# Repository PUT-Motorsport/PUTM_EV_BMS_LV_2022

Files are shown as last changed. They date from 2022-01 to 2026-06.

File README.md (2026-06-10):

# PUTM_EV_BMS_LV

## About
Battery Management System (BMS) is an electronic system that manages a rechargeable battery. In case of this project, it will be battery made of 21700 cells packed in 6S2P configuration.

## Tasks of Battery Management System:
- Voltage Measurement on every cell
- Current Measurement
- Temperature Measurement
- State of Charge calculate
- Charge Management with Cell Balance System
- Error Handling based on FSG Rules
- CAN - CAR communication
- Serial data print through USB

## Block diagram of the firmware

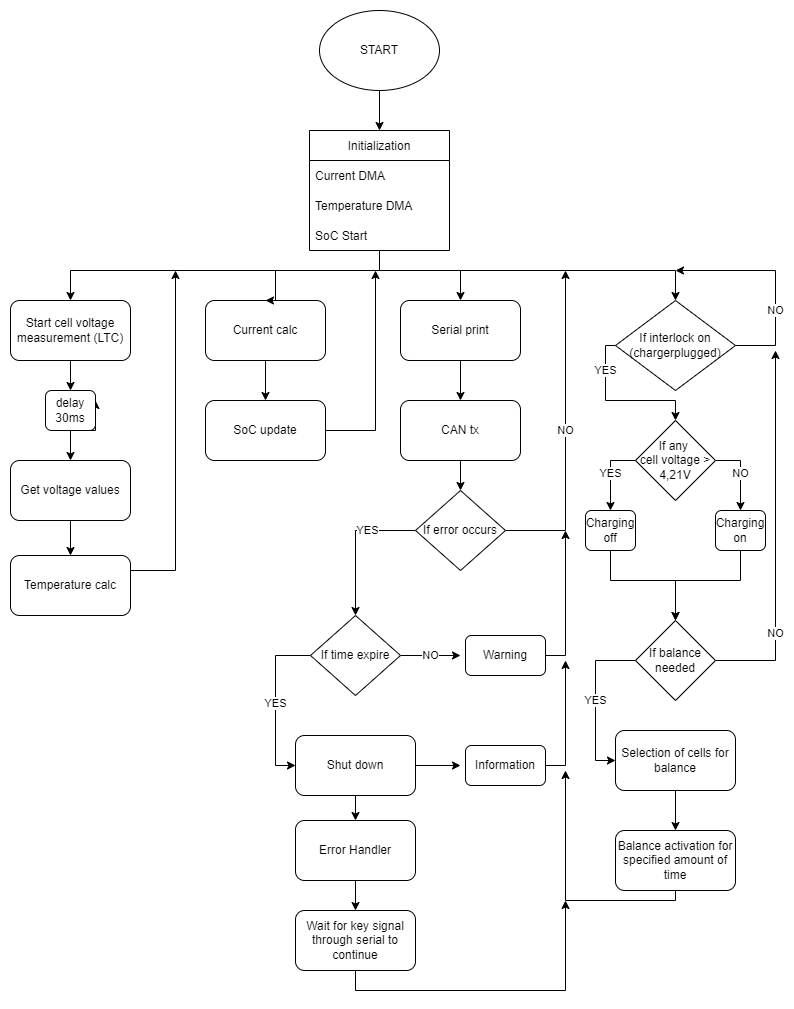
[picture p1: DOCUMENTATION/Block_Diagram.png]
diagram


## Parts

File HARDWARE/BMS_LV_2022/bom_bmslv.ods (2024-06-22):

Name | Value | Qty
Cell | 21700 | 12
Capacitor | 100nF | 22
Capacitor | 22pF | 2
Capacitor | 10uF | 2
Capacitor | 1uF | 7
Capacitor | 10nF | 7
Capacitor | 330pF | 1
Capacitor | 47nF | 1
Capacitor | 2.2uF | 1
Capacitor | 100uF | 1
Capacitor | 1nF | 1
LED | LED_RED | 10
Diode | PESD2CAN.215 | 1
Diode | D_Zener 9.1V | 6
Diode | D_TVS | 1
Diode | D_Schottky | 1
Fuse | PPTC 200mA | 1
Fuse Holder | Fuse Holder 10A | 2
Fuse | Fuse 10A
Ferrite Bead | 60R@100MHz | 3
Connector | USB-C_GCT_USB4145-03-0070-C | 1
Connector | D38999/20WD97SN | 1
Connector | B9B-XH-A (LF)(SN) | 1
Connector | XHP-9 | 1
Connector | 200-FTSH-107-01-L-DV-K-A | 1
Connector | B7B-XH-A (LF)(SN) | 1
Connector | XHP-7 | 1
Inductor | 10uH | 1
Inductor | 22uH | 1
LTC68101 | LTC6810-2 | 1
Transistor | BC846 | 1
Transistor | ZXMN3F30FHTA | 6
Transistor | SiSS05DN | 4
Transistor | BSS138 | 1
Resistor | 100k | 2
Resistor | 470 | 4
Resistor | 120 | 1
Resistor | 30 | 4
Resistor | 100 | 11
Resistor | 10k | 11
Resistor | 1k | 8
Resistor | 2.2k | 4
Resistor | 10 | 12
Resistor | 330 | 6
Resistor | 88.7k | 1
Resistor | 22.1k | 1
Resistor | 20k | 1
Resistor | 2.7k | 1
Resistor | 2k | 1
Resistor | 5.1k | 2
Tactile Switch | B3U-3000PM | 1
Thermistor_NTC | B57861S0103F040 | 8
MCU | STM32L4P5RET6 | 1
Switching Voltage Regulators | LD3985M33R_TSOT23 | 1
LDO | LMR23610 | 1
CAN transceiver | ATA6561-GAQW-N | 1
Current Sensor | ACHS-7123 | 1
Quartz Crystal | Quartz 16MHz | 1

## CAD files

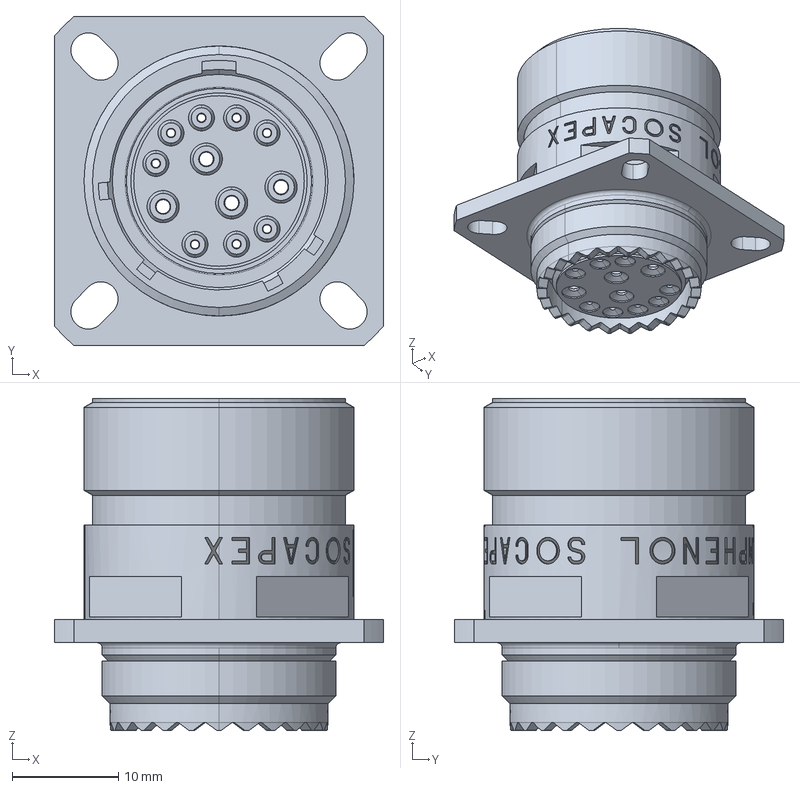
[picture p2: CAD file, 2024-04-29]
HARDWARE/BMS_LV_2022/3Dmodels/tvp00rw15-97p.stp
31.0 x 31.0 x 31.3 mm

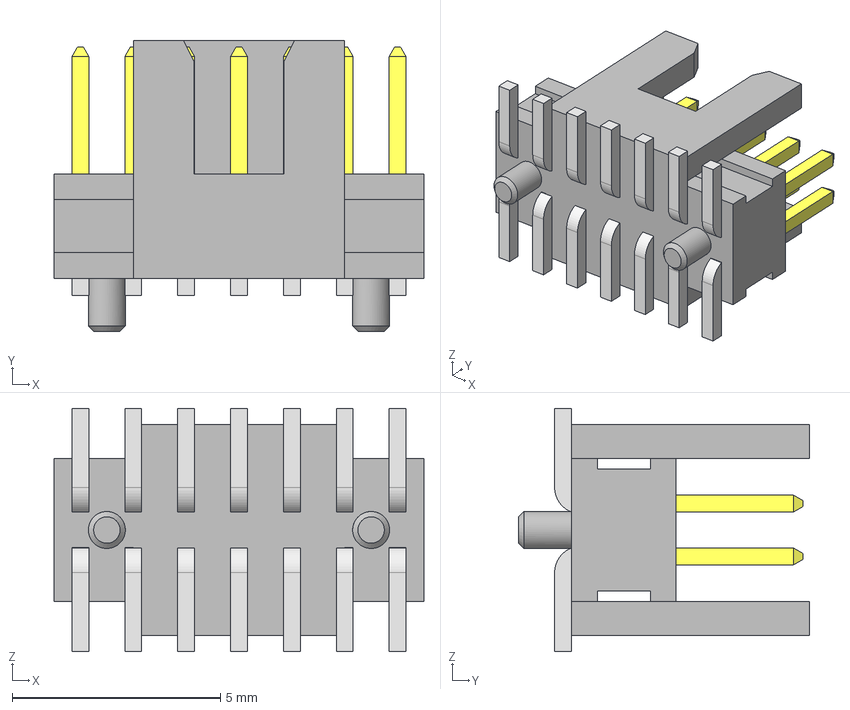
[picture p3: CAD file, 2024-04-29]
HARDWARE/BMS_LV_2022/3Dmodels/FTSH-107-01-L-DV-K-A.stp
8.89 x 6.98 x 5.84 mm
FTSH-107-01-L-DV-K-A_pins2
FTSH-107-01-L-DV-K-A_pins1
FTSH-107-01-L-DV-K-A_body

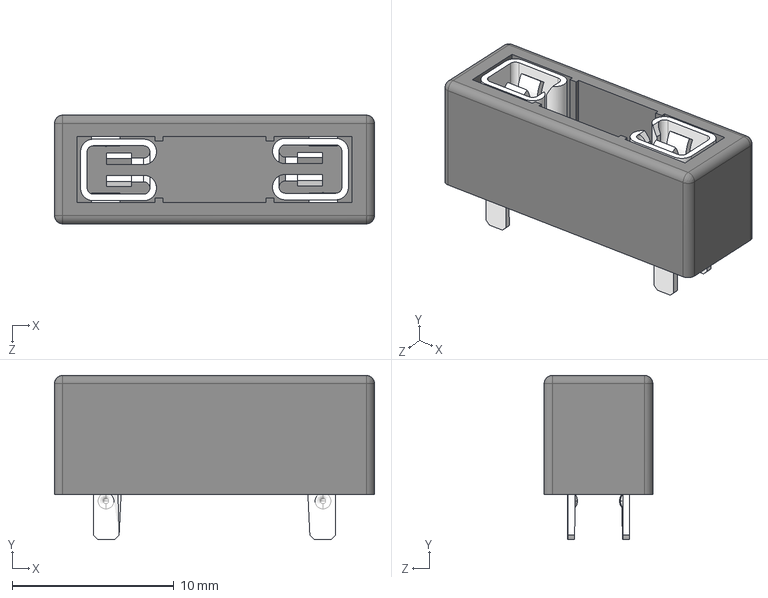
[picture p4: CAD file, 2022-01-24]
HARDWARE/BMS_LV_2022/3Dmodels/3557-2.stp
19.8 x 10.2 x 6.73 mm

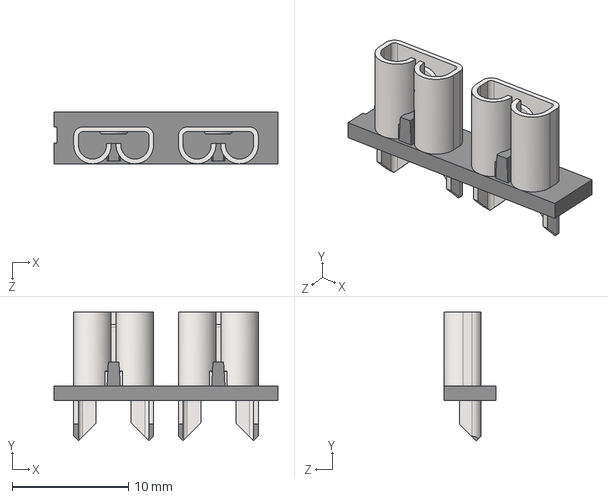
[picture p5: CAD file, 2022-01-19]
HARDWARE/BMS_LV_2022/3Dmodels/3522-2.stp
19.3 x 11.1 x 4.44 mm

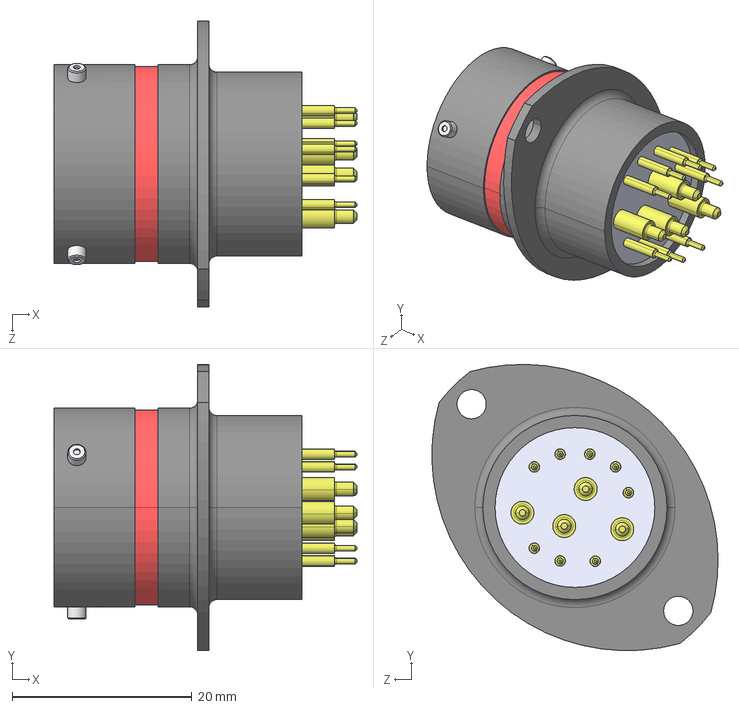
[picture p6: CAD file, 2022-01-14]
HARDWARE/BMS_LV_2022/3Dmodels/AS214-97PN.STEP
33.7 x 31.8 x 31.8 mm

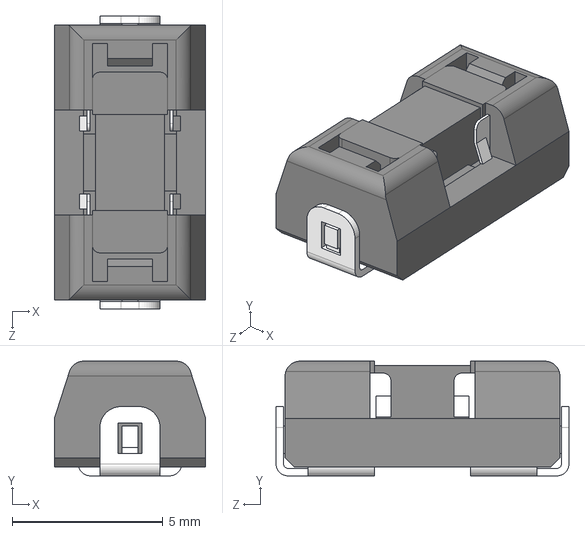
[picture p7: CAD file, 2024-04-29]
HARDWARE/BMS_LV_2022/3Dmodels/0154010.DR.stp
5.03 x 3.81 x 9.73 mm

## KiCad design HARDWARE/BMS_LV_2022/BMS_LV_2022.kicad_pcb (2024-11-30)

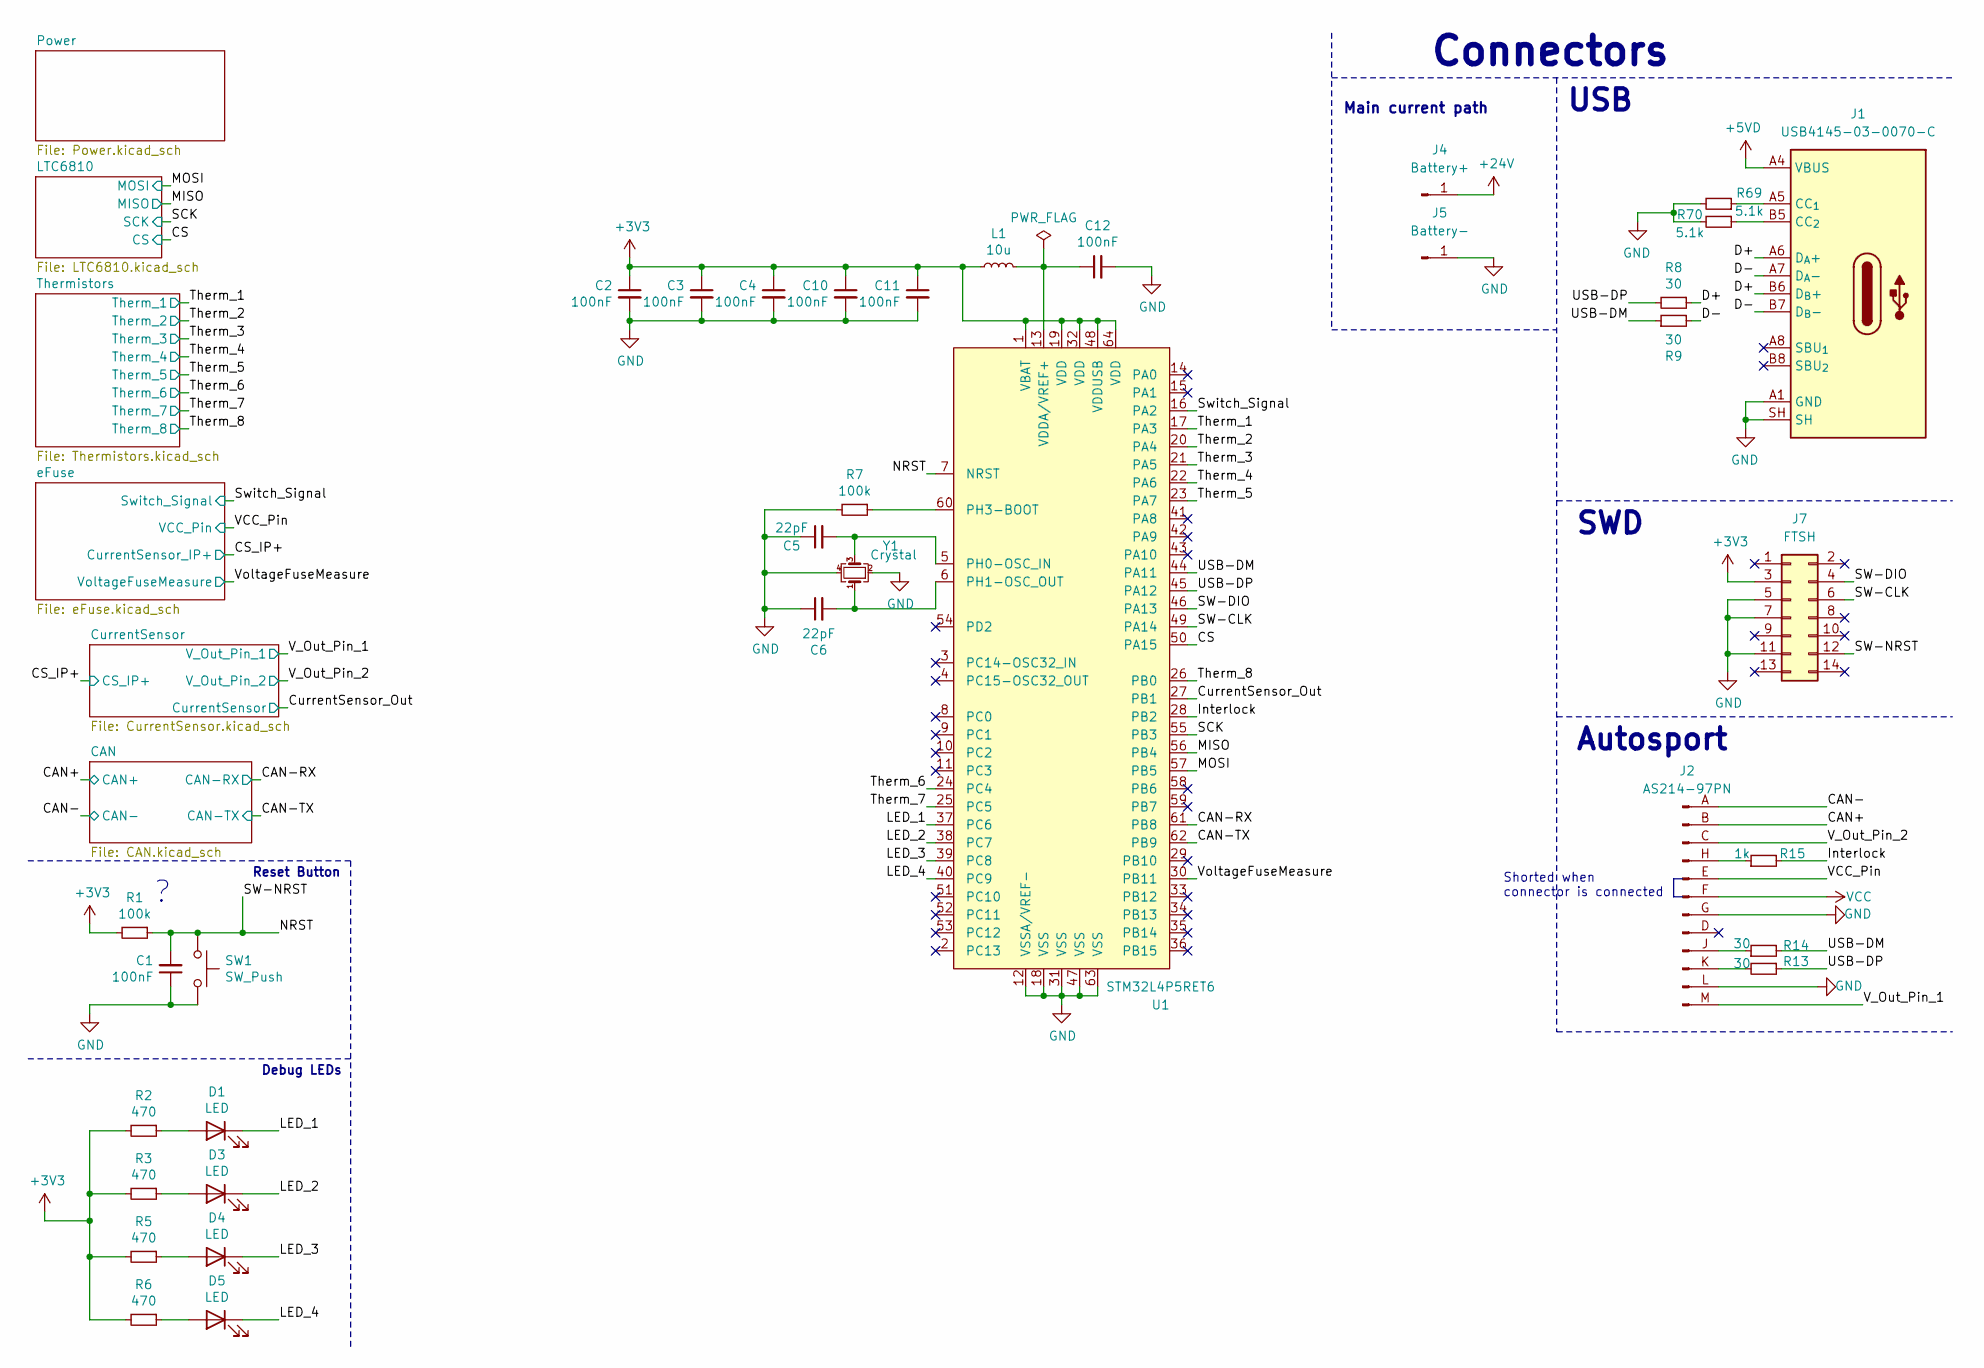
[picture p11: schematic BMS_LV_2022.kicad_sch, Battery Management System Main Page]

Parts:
C1, C2, C3, C4, C10, C11, C12: 100nF; C_0603_1608Metric
C5, C6: 22pF; C_0603_1608Metric
D1, D3, D4, D5: LED; LED_0603_1608Metric
J1: USB-C_GCT_USB4145-03-0070-C; USB-C_Receptacle_GCT_USB4145-03-0070-C; MPN USB4145-03-0070-C
J2: AS214-97PN
J4: Battery+; CellPad
J5: Battery-; CellPad
J7: FTSH; FTSH-107-XX-YYY-DV-K-A; Mouser Part Number 200-FTSH10701LDVKA
L1: 10u; L_0603_1608Metric
R1, R7: 100k; R_0603_1608Metric
R2, R3, R5, R6: 470; R_0603_1608Metric
R8, R9, R13, R14: 30; R_0603_1608Metric
R15: 1k; R_0603_1608Metric
R69, R70: 5.1k; R_0603_1608Metric
SW1: SW_Push; SW_SPST_B3U-1000P; Part Number B3U-1000PM
U1: STM32L4P5RET6; LQFP-64_10x10mm_P0.5mm
Y1: Crystal; Crystal_SMD_3225-4Pin_3.2x2.5mm

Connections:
+3V3: C2.1, C3.1, C4.1, C10.1, C11.1, J7.3, L1.2, R1.2, R2.2, R3.2, R5.2, R6.2, U1.1 (VBAT), U1.19 (VDD), U1.32 (VDD), U1.48 (VDDUSB), U1.64 (VDD); also elsewhere on the board
+5VD: J1.A4 (VBUS), J1.A9 (VBUS), J1.B4 (VBUS), J1.B9 (VBUS); also elsewhere on the board
+24V: J4.1; also elsewhere on the board
/CAN+: J2.B; also elsewhere on the board
/CAN-: J2.A; also elsewhere on the board
/CAN-RX: U1.61 (PB8); also elsewhere on the board
/CAN-TX: U1.62 (PB9); also elsewhere on the board
/CS: U1.50 (PA15); also elsewhere on the board
/CurrentSensor_Out: U1.27 (PB1); also elsewhere on the board
/D+: J1.A6 (D_{A}+), J1.B6 (D_{B}+), R8.1
/D-: J1.A7 (D_{A}-), J1.B7 (D_{B}-), R9.2
/Interlock: R15.2, U1.28 (PB2)
/LED_1: D1.1 (K), U1.37 (PC6)
/LED_2: D3.1 (K), U1.38 (PC7)
/LED_3: D4.1 (K), U1.39 (PC8)
/LED_4: D5.1 (K), U1.40 (PC9)
/MISO: U1.56 (PB4); also elsewhere on the board
/MOSI: U1.57 (PB5); also elsewhere on the board
/NRST: C1.2, J7.12, R1.1, SW1.1, U1.7 (NRST)
/SCK: U1.55 (PB3); also elsewhere on the board
/SW-CLK: J7.6, U1.49 (PA14)
/SW-DIO: J7.4, U1.46 (PA13)
/Switch_Signal: U1.16 (PA2); also elsewhere on the board
/Therm_1: U1.17 (PA3); also elsewhere on the board
/Therm_2: U1.20 (PA4); also elsewhere on the board
/Therm_3: U1.21 (PA5); also elsewhere on the board
/Therm_4: U1.22 (PA6); also elsewhere on the board
/Therm_5: U1.23 (PA7); also elsewhere on the board
/Therm_6: U1.24 (PC4); also elsewhere on the board
/Therm_7: U1.25 (PC5); also elsewhere on the board
/Therm_8: U1.26 (PB0); also elsewhere on the board
/USB-DM: R9.1, R14.2, U1.44 (PA11)
/USB-DP: R8.2, R13.1, U1.45 (PA12)
/VCC_Pin: J2.E; also elsewhere on the board
/V_Out_Pin_1: J2.M; also elsewhere on the board
/V_Out_Pin_2: J2.C; also elsewhere on the board
/VoltageFuseMeasure: U1.30 (PB11); also elsewhere on the board
GND: C1.1, C2.2, C3.2, C4.2, C5.1, C6.1, C10.2, C11.2, C12.2, J1.A1 (GND), J1.A12 (GND), J1.B1 (GND), J1.B12 (GND), J1.SH, J2.G, J2.L, J5.1, J7.5, J7.7, J7.11, R7.2, R69.2, R70.2, SW1.2, U1.12 (VSSA/VREF-), U1.18 (VSS), U1.31 (VSS), U1.47 (VSS), U1.63 (VSS), Y1.2, Y1.4; also elsewhere on the board
unnamed: D1.2 (A), R2.1
unnamed: D3.2 (A), R3.1
unnamed: D4.2 (A), R5.1
unnamed: D5.2 (A), R6.1
unnamed: J1.A5 (CC_{1}), R69.1
unnamed: J1.B5 (CC_{2}), R70.1
unnamed: J2.H, R15.1
unnamed: J2.J, R14.1
unnamed: J2.K, R13.2
unnamed: C5.2, U1.5 (PH0-OSC_IN), Y1.3
unnamed: C6.2, U1.6 (PH1-OSC_OUT), Y1.1
unnamed: R7.1, U1.60 (PH3-BOOT)
unnamed: C12.1, L1.1, U1.13 (VDDA/VREF+)
VCC: J2.F; also elsewhere on the board

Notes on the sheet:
SWD
USB
Debug LEDs
Reset Button
Main current path
Shorted when connector is connected
Connectors
Autosport

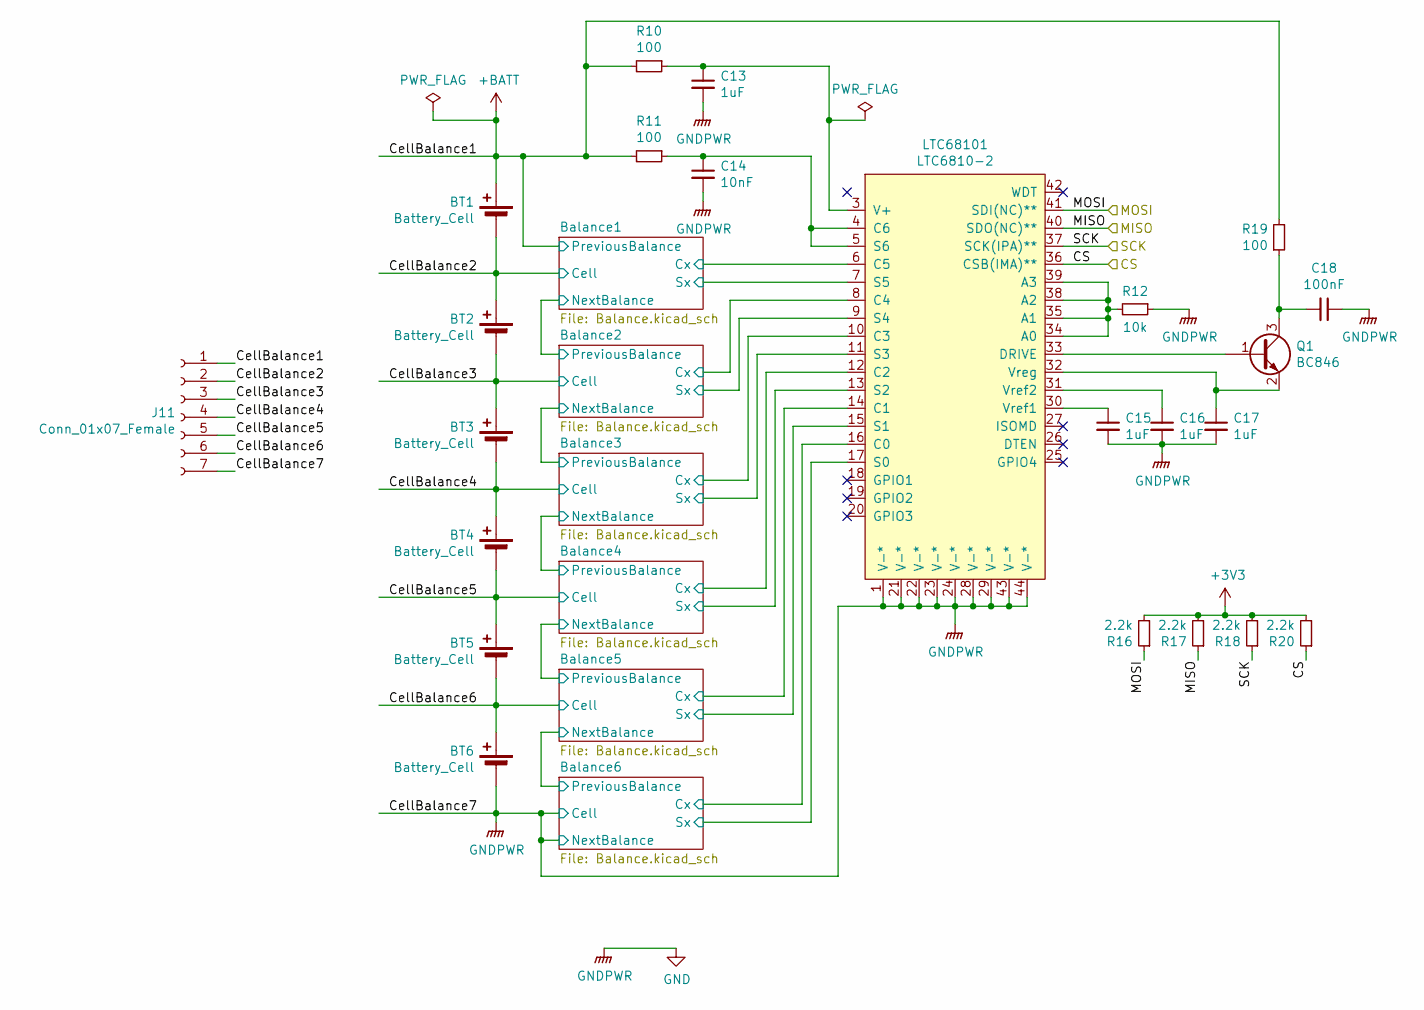
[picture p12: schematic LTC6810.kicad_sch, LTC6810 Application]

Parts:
BT1, BT2, BT3, BT4, BT5, BT6: Battery_Cell
C13, C15, C16, C17: 1uF; C_0603_1608Metric
C14: 10nF; C_0603_1608Metric
C18: 100nF; C_0603_1608Metric
J11: Conn_01x07_Female; JST_XH_B7B-XH-A_1x07_P2.50mm_Vertical
LTC68101: LTC6810-2; LTC6810
Q1: BC846; SOT-23
R10, R11, R19: 100; R_0603_1608Metric
R12: 10k; R_0603_1608Metric
R16, R17, R18, R20: 2.2k; R_0603_1608Metric

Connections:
+3V3: R16.2, R17.2, R18.2, R20.2; also elsewhere on the board
+BATT: BT1.1 (+), J11.1, R10.2, R11.2, R19.2; also elsewhere on the board
/CS: LTC68101.36 (CSB(IMA)**), R20.1; also elsewhere on the board
/LTC6810/Balance1/Cx: LTC68101.6 (C5); also elsewhere on the board
/LTC6810/Balance1/Sx: LTC68101.7 (S5); also elsewhere on the board
/LTC6810/Balance2/Cx: LTC68101.8 (C4); also elsewhere on the board
/LTC6810/Balance2/Sx: LTC68101.9 (S4); also elsewhere on the board
/LTC6810/Balance3/Cx: LTC68101.10 (C3); also elsewhere on the board
/LTC6810/Balance3/Sx: LTC68101.11 (S3); also elsewhere on the board
/LTC6810/Balance4/Cx: LTC68101.12 (C2); also elsewhere on the board
/LTC6810/Balance4/Sx: LTC68101.13 (S2); also elsewhere on the board
/LTC6810/Balance5/Cx: LTC68101.14 (C1); also elsewhere on the board
/LTC6810/Balance5/Sx: LTC68101.15 (S1); also elsewhere on the board
/LTC6810/Balance6/Cx: LTC68101.16 (C0); also elsewhere on the board
/LTC6810/Balance6/Sx: LTC68101.17 (S0); also elsewhere on the board
/LTC6810/CellBalance2: BT1.2 (-), BT2.1 (+), J11.2; also elsewhere on the board
/LTC6810/CellBalance3: BT2.2 (-), BT3.1 (+), J11.3; also elsewhere on the board
/LTC6810/CellBalance4: BT3.2 (-), BT4.1 (+), J11.4; also elsewhere on the board
/LTC6810/CellBalance5: BT4.2 (-), BT5.1 (+), J11.5; also elsewhere on the board
/LTC6810/CellBalance6: BT5.2 (-), BT6.1 (+), J11.6; also elsewhere on the board
/MISO: LTC68101.40 (SDO(NC)**), R17.1; also elsewhere on the board
/MOSI: LTC68101.41 (SDI(NC)**), R16.1; also elsewhere on the board
/SCK: LTC68101.37 (SCK(IPA)**), R18.1; also elsewhere on the board
GND: BT6.2 (-), C13.2, C14.2, C15.2, C16.2, C17.2, C18.1, J11.7, LTC68101.1 (V-*), LTC68101.21 (V-*), LTC68101.22 (V-*), LTC68101.23 (V-*), LTC68101.24 (V-*), LTC68101.28 (V-*), LTC68101.29 (V-*), LTC68101.43 (V-*), LTC68101.44 (V-*), R12.1; also elsewhere on the board
unnamed: LTC68101.34 (A0), LTC68101.35 (A1), LTC68101.38 (A2), LTC68101.39 (A3), R12.2
unnamed: C14.1, LTC68101.4 (C6), LTC68101.5 (S6), R11.1
unnamed: LTC68101.33 (DRIVE), Q1.1 (B)
unnamed: C13.1, LTC68101.3 (V+), R10.1
unnamed: C15.1, LTC68101.30 (Vref1)
unnamed: C16.1, LTC68101.31 (Vref2)
unnamed: C17.1, LTC68101.32 (Vreg), Q1.2 (E)
unnamed: C18.2, Q1.3 (C), R19.1

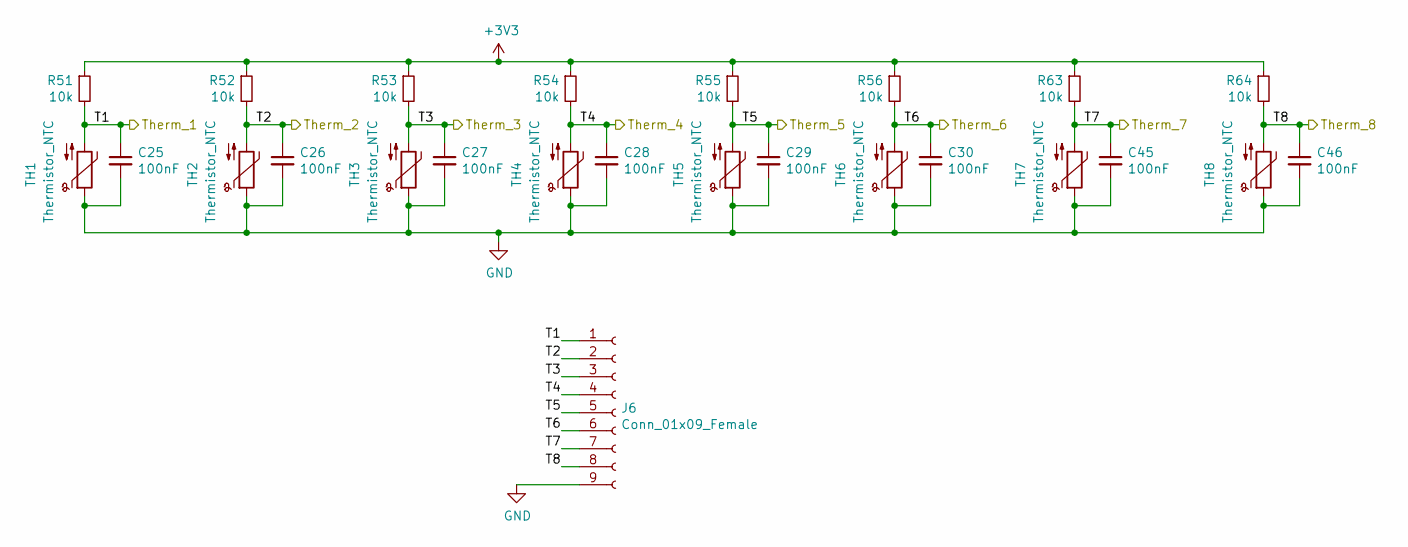
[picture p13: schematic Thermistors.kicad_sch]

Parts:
C25, C26, C27, C28, C29, C30, C45, C46: 100nF; C_0603_1608Metric
J6: Conn_01x09_Female; JST_XH_B9B-XH-A_1x09_P2.50mm_Vertical
R51, R52, R53, R54, R55, R56, R63, R64: 10k; R_0603_1608Metric
TH1, TH2, TH3, TH4, TH5, TH6, TH7, TH8: Thermistor_NTC

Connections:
+3V3: R51.1, R52.1, R53.1, R54.1, R55.1, R56.1, R63.1, R64.1; also elsewhere on the board
/Therm_1: C25.1, J6.1, R51.2, TH1.2; also elsewhere on the board
/Therm_2: C26.1, J6.2, R52.2, TH2.2; also elsewhere on the board
/Therm_3: C27.1, J6.3, R53.2, TH3.2; also elsewhere on the board
/Therm_4: C28.1, J6.4, R54.2, TH4.2; also elsewhere on the board
/Therm_5: C29.1, J6.5, R55.2, TH5.2; also elsewhere on the board
/Therm_6: C30.1, J6.6, R56.2, TH6.2; also elsewhere on the board
/Therm_7: C45.1, J6.7, R63.2, TH7.2; also elsewhere on the board
/Therm_8: C46.1, J6.8, R64.2, TH8.2; also elsewhere on the board
GND: C25.2, C26.2, C27.2, C28.2, C29.2, C30.2, C45.2, C46.2, J6.9, TH1.1, TH2.1, TH3.1, TH4.1, TH5.1, TH6.1, TH7.1, TH8.1; also elsewhere on the board

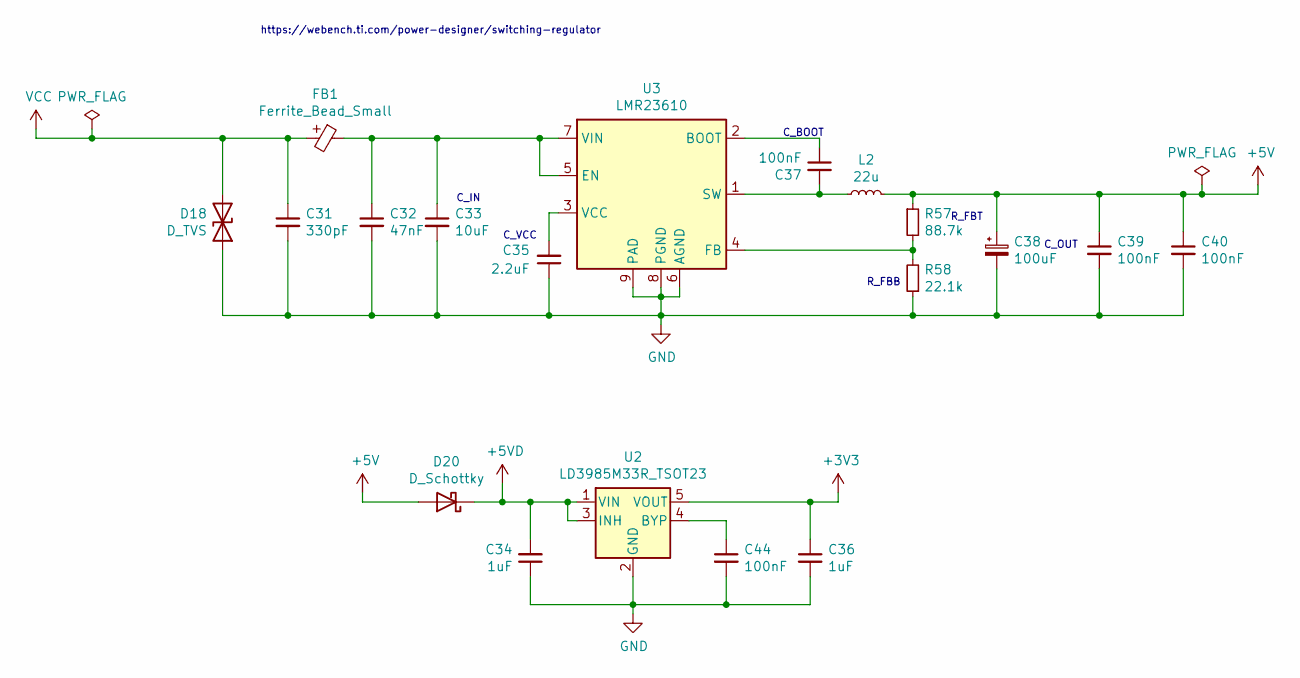
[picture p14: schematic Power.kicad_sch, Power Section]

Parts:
C31: 330pF; C_0603_1608Metric
C32: 47nF; C_0603_1608Metric
C33: 10uF; C_0603_1608Metric
C34, C36: 1uF; C_0603_1608Metric
C35: 2.2uF; C_0603_1608Metric
C37, C39, C40, C44: 100nF; C_0603_1608Metric
C38: 100uF; CP_EIA-6032-28_Kemet-C; Part Number TPSC107K010R0100
D18: D_TVS; D_SMB
D20: D_Schottky; D_SOD-123; Part Number SD103BW
FB1: Ferrite_Bead_Small; L_0603_1608Metric
L2: 22u; L_7.3x7.3_H4.5; Part Number 7447779122
R57: 88.7k; R_0603_1608Metric
R58: 22.1k; R_0603_1608Metric
U2: LD3985M33R_TSOT23; TSOT-23-5; Part Number LDS3985M33R
U3: LMR23610; Texas_HSOP-8-1EP_3.9x4.9mm_P1.27mm_ThermalVias

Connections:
+3V3: C36.1, U2.5 (VOUT); also elsewhere on the board
+5V: C38.1, C39.1, C40.1, D20.2 (A), L2.2, R57.1; also elsewhere on the board
+5VD: C34.2, D20.1 (K), U2.1 (VIN), U2.3 (INH); also elsewhere on the board
GND: C31.2, C32.2, C33.2, C34.1, C35.1, C36.2, C38.2, C39.2, C40.2, C44.2, D18.1 (A1), R58.1, U2.2 (GND), U3.6 (AGND), U3.8 (PGND), U3.9 (PAD); also elsewhere on the board
unnamed: C44.1, U2.4 (BYP)
unnamed: C37.1, U3.2 (BOOT)
unnamed: C32.1, C33.1, FB1.1, U3.5 (EN), U3.7 (VIN)
unnamed: R57.2, R58.2, U3.4 (FB)
unnamed: C37.2, L2.1, U3.1 (SW)
unnamed: C35.2, U3.3 (VCC)
VCC: C31.1, D18.2 (A2), FB1.2; also elsewhere on the board

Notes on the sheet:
C_BOOT
https://webench.ti.com/power-designer/switching-regulator
C_IN
R_FBB
R_FBT
C_VCC
C_OUT

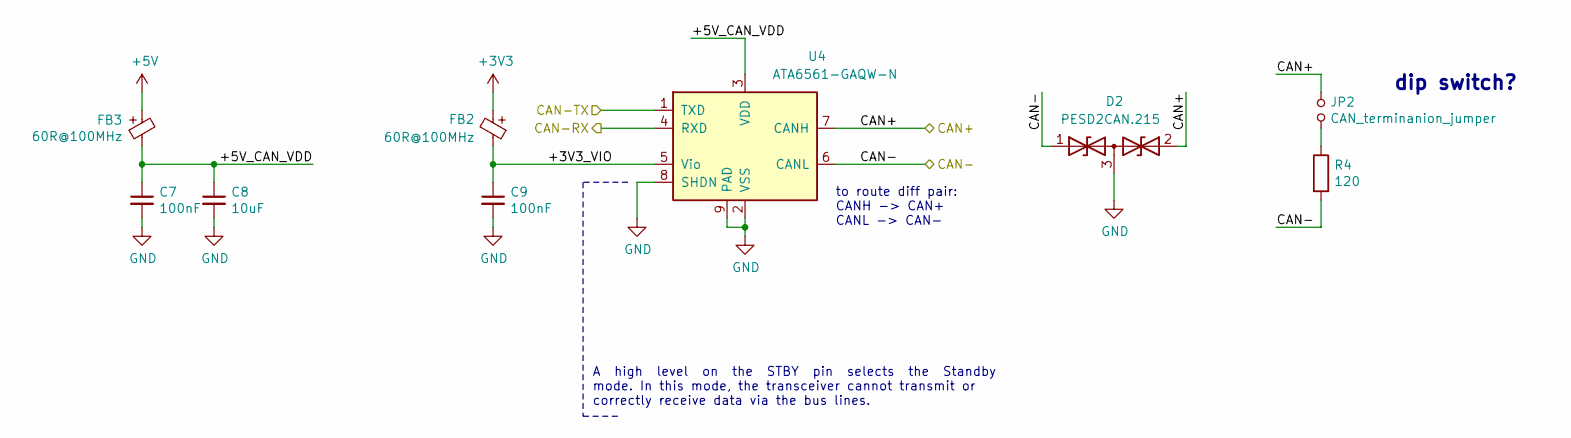
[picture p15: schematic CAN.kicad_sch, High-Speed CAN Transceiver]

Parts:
C7, C9: 100nF; C_0603_1608Metric
C8: 10uF; C_0603_1608Metric
D2: PESD2CAN.215; SOT-23
FB2, FB3: 60R@100MHz; L_0603_1608Metric
JP2: CAN_terminanion_jumper; SolderJumper-2_P1.3mm_Open_TrianglePad1.0x1.5mm
R4: 120; R_0603_1608Metric
U4: ATA6561-GAQW-N; SOIC-8_3.9x4.9mm_P1.27mm

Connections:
+3V3: FB2.2; also elsewhere on the board
+5V: FB3.2; also elsewhere on the board
/CAN+: D2.2 (A2), JP2.1, U4.7 (CANH); also elsewhere on the board
/CAN-: D2.1 (A1), R4.2, U4.6 (CANL); also elsewhere on the board
/CAN-RX: U4.4 (RXD); also elsewhere on the board
/CAN-TX: U4.1 (TXD); also elsewhere on the board
/CAN/+3V3_VIO: C9.1, FB2.1, U4.5 (Vio)
/CAN/+5V_CAN_VDD: C7.1, C8.1, FB3.1, U4.3 (VDD)
GND: C7.2, C8.2, C9.2, D2.3 (common), U4.2 (VSS), U4.8 (SHDN), U4.9 (PAD); also elsewhere on the board
unnamed: JP2.2, R4.1

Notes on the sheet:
dip switch?
A high level on the STBY pin selects the Standby mode. In this mode, the transceiver cannot transmit or correctly receive data via the bus lines.
to route diff pair: CANH -> CAN+ CANL -> CAN-

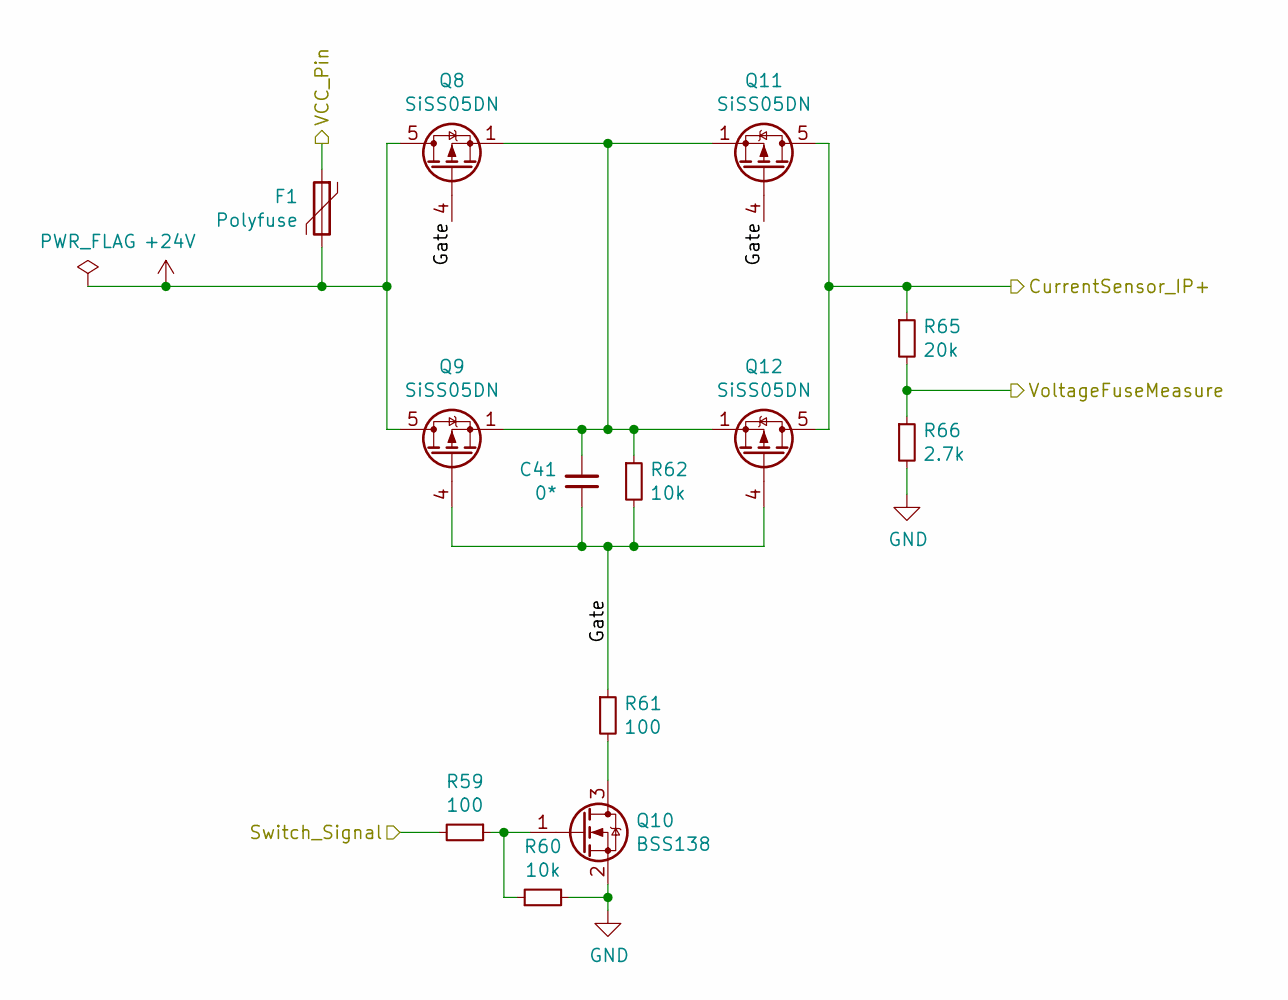
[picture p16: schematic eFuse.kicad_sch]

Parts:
C41: 0*; C_0603_1608Metric
F1: Polyfuse; Fuse_1206_3216Metric; Part Number 0ZCJ0020FF2E
Q8, Q9, Q11, Q12: SiSS05DN; Vishay_PowerPAK_1212-8_Single; Part Number SISS05DN-T1-GE3
Q10: BSS138; SOT-23
R59, R61: 100; R_0603_1608Metric
R60, R62: 10k; R_0603_1608Metric
R65: 20k; R_0603_1608Metric
R66: 2.7k; R_0603_1608Metric

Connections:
+24V: F1.2, Q8.5 (D), Q9.5 (D); also elsewhere on the board
/CS_IP+: Q11.5 (D), Q12.5 (D), R65.1; also elsewhere on the board
/Switch_Signal: R59.2; also elsewhere on the board
/VCC_Pin: F1.1; also elsewhere on the board
/VoltageFuseMeasure: R65.2, R66.1; also elsewhere on the board
/eFuse/Gate: C41.1, Q8.4 (G), Q9.4 (G), Q11.4 (G), Q12.4 (G), R61.1, R62.2
GND: Q10.2 (S), R60.2, R66.2; also elsewhere on the board
unnamed: C41.2, Q8.1 (S), Q8.2 (S), Q8.3 (S), Q9.1 (S), Q9.2 (S), Q9.3 (S), Q11.1 (S), Q11.2 (S), Q11.3 (S), Q12.1 (S), Q12.2 (S), Q12.3 (S), R62.1
unnamed: Q10.3 (D), R61.2
unnamed: Q10.1 (G), R59.1, R60.1

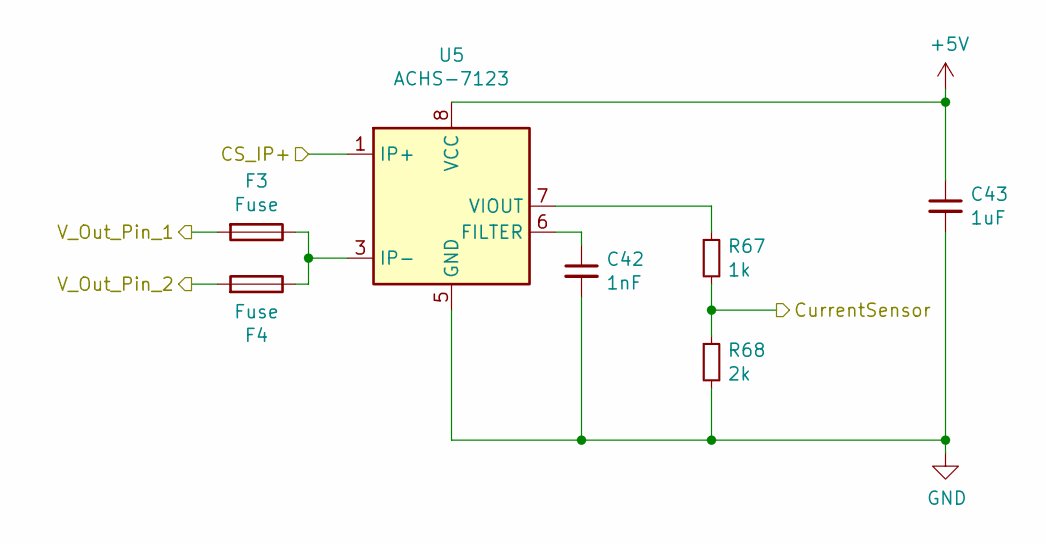
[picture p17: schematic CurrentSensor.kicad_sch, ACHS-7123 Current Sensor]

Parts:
C42: 1nF; C_0603_1608Metric
C43: 1uF; C_0603_1608Metric
F3, F4: Fuse; 0154001.DRT; Part Number 0154010.DR
R67: 1k; R_0603_1608Metric
R68: 2k; R_0603_1608Metric
U5: ACHS-7123; SOIC-8_3.9x4.9mm_P1.27mm

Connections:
+5V: C43.1, U5.8 (VCC); also elsewhere on the board
/CS_IP+: U5.1 (IP+), U5.2 (IP+); also elsewhere on the board
/CurrentSensor_Out: R67.2, R68.1; also elsewhere on the board
/V_Out_Pin_1: F3.2; also elsewhere on the board
/V_Out_Pin_2: F4.2; also elsewhere on the board
GND: C42.2, C43.2, R68.2, U5.5 (GND); also elsewhere on the board
unnamed: F3.1, F4.1, U5.3 (IP-), U5.4 (IP-)
unnamed: C42.1, U5.6 (FILTER)
unnamed: R67.1, U5.7 (VIOUT)

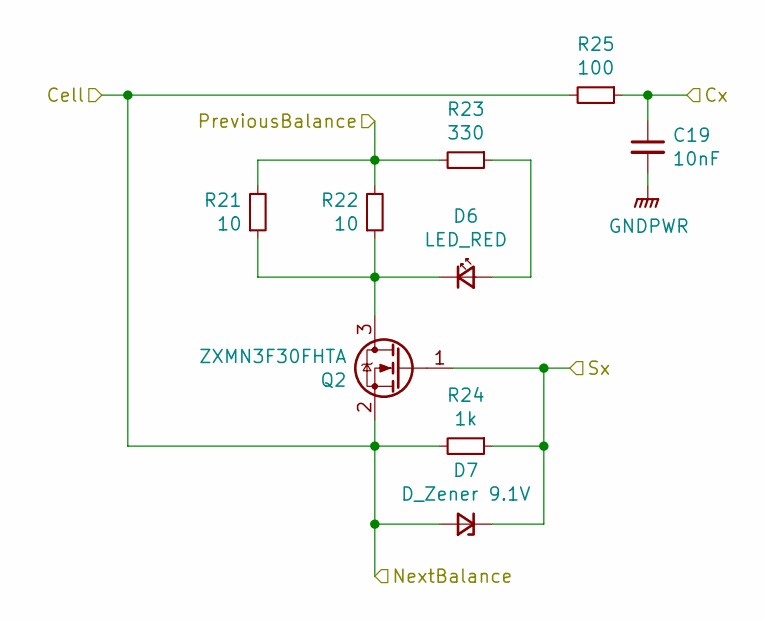
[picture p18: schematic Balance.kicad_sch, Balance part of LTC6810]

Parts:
C19: 10nF; C_0603_1608Metric
D6: LED_RED; LED_0603_1608Metric
D7: D_Zener 9.1V; D_SOD-323; Part Number BZX384-C9V1.115
Q2: ZXMN3F30FHTA; SOT-23
R21, R22: 10; R_2512_6332Metric; Part Number CHP2512AFX-10R0ELF
R23: 330; R_0603_1608Metric
R24: 1k; R_0603_1608Metric
R25: 100; R_0603_1608Metric

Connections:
+BATT: R21.2, R22.2, R23.2; also elsewhere on the board
/LTC6810/Balance1/Cx: C19.1, R25.1; also elsewhere on the board
/LTC6810/Balance1/Sx: D7.1 (K), Q2.1 (G), R24.1; also elsewhere on the board
/LTC6810/CellBalance2: D7.2 (A), Q2.2 (S), R24.2, R25.2; also elsewhere on the board
GND: C19.2; also elsewhere on the board
unnamed: D6.2 (A), R23.1
unnamed: D6.1 (K), Q2.3 (D), R21.1, R22.1

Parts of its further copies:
C20, C21, C22, C23, C24: 10nF; C_0603_1608Metric
D8, D10, D12, D14, D16: LED_RED; LED_0603_1608Metric
D9, D11, D13, D15, D17: D_Zener 9.1V; D_SOD-323; Part Number BZX384-C9V1.115
Q3, Q4, Q5, Q6, Q7: ZXMN3F30FHTA; SOT-23
R26, R27, R31, R32, R36, R37, R41, R42, R46, R47: 10; R_2512_6332Metric; Part Number CHP2512AFX-10R0ELF
R28, R33, R38, R43, R48: 330; R_0603_1608Metric
R29, R34, R39, R44, R49: 1k; R_0603_1608Metric
R30, R35, R40, R45, R50: 100; R_0603_1608Metric

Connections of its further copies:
/LTC6810/Balance2/Cx: C20.1, R30.1; also elsewhere on the board
/LTC6810/Balance2/Sx: D9.1 (K), Q3.1 (G), R29.1; also elsewhere on the board
/LTC6810/Balance3/Cx: C21.1, R35.1; also elsewhere on the board
/LTC6810/Balance3/Sx: D11.1 (K), Q4.1 (G), R34.1; also elsewhere on the board
/LTC6810/Balance4/Cx: C22.1, R40.1; also elsewhere on the board
/LTC6810/Balance4/Sx: D13.1 (K), Q5.1 (G), R39.1; also elsewhere on the board
/LTC6810/Balance5/Cx: C23.1, R45.1; also elsewhere on the board
/LTC6810/Balance5/Sx: D15.1 (K), Q6.1 (G), R44.1; also elsewhere on the board
/LTC6810/Balance6/Cx: C24.1, R50.1; also elsewhere on the board
/LTC6810/Balance6/Sx: D17.1 (K), Q7.1 (G), R49.1; also elsewhere on the board
/LTC6810/CellBalance2: R26.2, R27.2, R28.2; also elsewhere on the board
/LTC6810/CellBalance3: D9.2 (A), Q3.2 (S), R29.2, R30.2, R31.2, R32.2, R33.2; also elsewhere on the board
/LTC6810/CellBalance4: D11.2 (A), Q4.2 (S), R34.2, R35.2, R36.2, R37.2, R38.2; also elsewhere on the board
/LTC6810/CellBalance5: D13.2 (A), Q5.2 (S), R39.2, R40.2, R41.2, R42.2, R43.2; also elsewhere on the board
/LTC6810/CellBalance6: D15.2 (A), Q6.2 (S), R44.2, R45.2, R46.2, R47.2, R48.2; also elsewhere on the board
GND: C20.2, C21.2, C22.2, C23.2, C24.2, D17.2 (A), Q7.2 (S), R49.2, R50.2; also elsewhere on the board
unnamed: D8.2 (A), R28.1
unnamed: D8.1 (K), Q3.3 (D), R26.1, R27.1
unnamed: D10.2 (A), R33.1
unnamed: D10.1 (K), Q4.3 (D), R31.1, R32.1
unnamed: D12.2 (A), R38.1
unnamed: D12.1 (K), Q5.3 (D), R36.1, R37.1
unnamed: D14.2 (A), R43.1
unnamed: D14.1 (K), Q6.3 (D), R41.1, R42.1
unnamed: D16.2 (A), R48.1
unnamed: D16.1 (K), Q7.3 (D), R46.1, R47.1

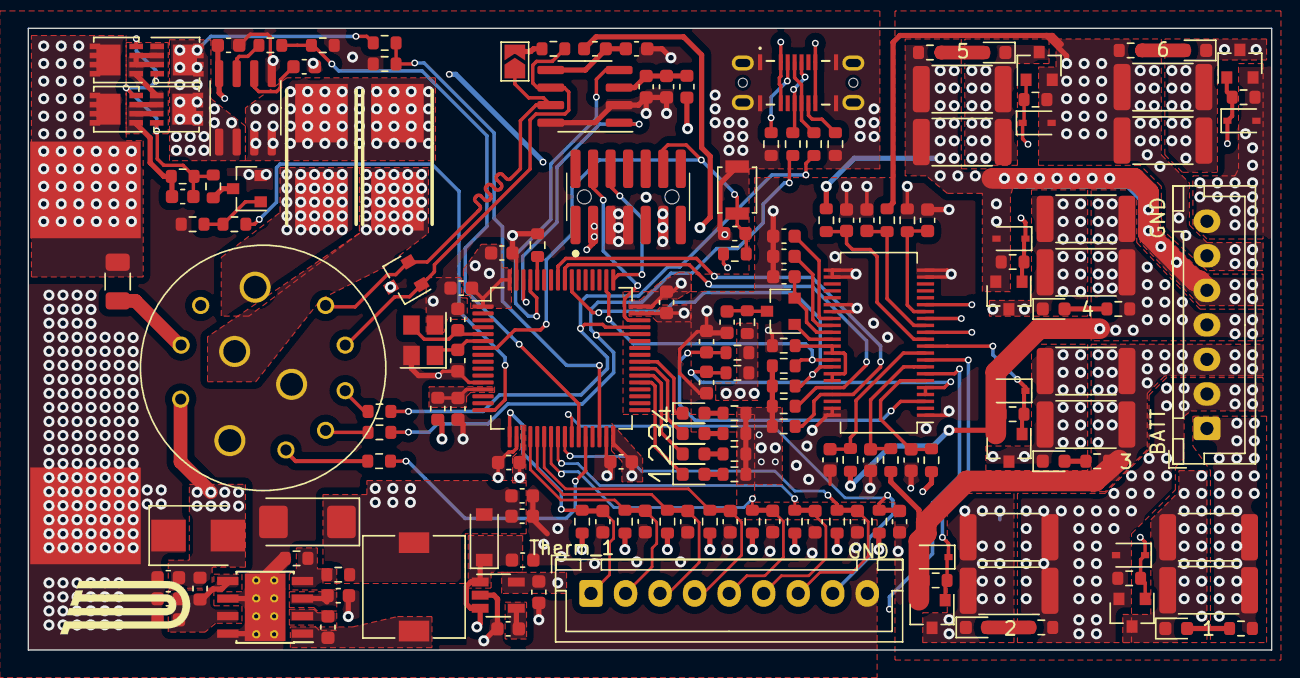
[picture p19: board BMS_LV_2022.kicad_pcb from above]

Board: 4 copper layers, 90.0 x 45.0 mm, 171 parts (1 on the bottom side), 108 nets.

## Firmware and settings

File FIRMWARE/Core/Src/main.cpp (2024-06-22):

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
/* Includes ------------------------------------------------------------------*/
#include "main.h"
#include "cmsis_os.h"
#include "usb_device.h"

/* USER CODE BEGIN Includes */
#include "soc_ekf.h"
#include <global_variables.hpp>
/* USER CODE END Includes */

typedef StaticTask_t osStaticThreadDef_t;
ADC_HandleTypeDef hadc1;
ADC_HandleTypeDef hadc2;
DMA_HandleTypeDef hdma_adc1;
DMA_HandleTypeDef hdma_adc2;

CAN_HandleTypeDef hcan1;

RTC_HandleTypeDef hrtc;

SPI_HandleTypeDef hspi1;

TIM_HandleTypeDef htim3;
TIM_HandleTypeDef htim6;
TIM_HandleTypeDef htim8;

/* Definitions for defaultTask */
osThreadId_t defaultTaskHandle;
const osThreadAttr_t defaultTask_attributes = {
  .name = "defaultTask",
  .stack_size = 512 * 4,
  .priority = (osPriority_t) osPriorityLow,
};
/* Definitions for ltc_task */
osThreadId_t ltc_taskHandle;
uint32_t ltc_taskBuffer[ 512 ];
osStaticThreadDef_t ltc_taskControlBlock;
const osThreadAttr_t ltc_task_attributes = {
  .name = "ltc_task",
  .cb_mem = &ltc_taskControlBlock,
  .cb_size = sizeof(ltc_taskControlBlock),
  .stack_mem = &ltc_taskBuffer[0],
  .stack_size = sizeof(ltc_taskBuffer),
  .priority = (osPriority_t) osPriorityNormal,
};
/* Definitions for soc_update_task */
osThreadId_t soc_update_taskHandle;
uint32_t soc_update_taskBuffer[ 512 ];
osStaticThreadDef_t soc_update_taskControlBlock;
const osThreadAttr_t soc_update_task_attributes = {
  .name = "soc_update_task",
  .cb_mem = &soc_update_taskControlBlock,
  .cb_size = sizeof(soc_update_taskControlBlock),
  .stack_mem = &soc_update_taskBuffer[0],
  .stack_size = sizeof(soc_update_taskBuffer),
  .priority = (osPriority_t) osPriorityBelowNormal,
};
/* Definitions for balance_task */
osThreadId_t balance_taskHandle;
uint32_t balance_taskBuffer[ 512 ];
osStaticThreadDef_t balance_taskControlBlock;
const osThreadAttr_t balance_task_attributes = {
  .name = "balance_task",
  .cb_mem = &balance_taskControlBlock,
  .cb_size = sizeof(balance_taskControlBlock),
  .stack_mem = &balance_taskBuffer[0],
  .stack_size = sizeof(balance_taskBuffer),
  .priority = (osPriority_t) osPriorityAboveNormal,
};
/* Definitions for comm_err_task */
osThreadId_t comm_err_taskHandle;
uint32_t comm_err_taskBuffer[ 512 ];
osStaticThreadDef_t comm_err_taskControlBlock;
const osThreadAttr_t comm_err_task_attributes = {
  .name = "comm_err_task",
  .cb_mem = &comm_err_taskControlBlock,
  .cb_size = sizeof(comm_err_taskControlBlock),
  .stack_mem = &comm_err_taskBuffer[0],
  .stack_size = sizeof(comm_err_taskBuffer),
  .priority = (osPriority_t) osPriorityHigh,
};
void SystemClock_Config(void);
static void MX_GPIO_Init(void);
static void MX_DMA_Init(void);
static void MX_ADC1_Init(void);
static void MX_ADC2_Init(void);
static void MX_CAN1_Init(void);
static void MX_RTC_Init(void);
static void MX_SPI1_Init(void);
static void MX_TIM3_Init(void);
static void MX_TIM6_Init(void);
static void MX_TIM8_Init(void);
void StartDefaultTask(void *argument);
extern void start_ltc_function(void *argument);
extern void start_soc_function(void *argument);
extern void start_balance_function(void *argument);
extern void start_comm_err_function(void *argument);

/**
  * @brief  The application entry point.
  * @retval int
  */
int main(void)
{

  /* MCU Configuration--------------------------------------------------------*/

  /* Reset of all peripherals, Initializes the Flash interface and the Systick. */
  HAL_Init();

  /* Configure the system clock */
  SystemClock_Config();

  /* Initialize all configured peripherals */
  MX_GPIO_Init();
  MX_DMA_Init();
  MX_ADC1_Init();
  MX_ADC2_Init();
  MX_CAN1_Init();
  MX_RTC_Init();
  MX_SPI1_Init();
  MX_TIM3_Init();
  MX_TIM6_Init();
  MX_TIM8_Init();
  /* Init scheduler */
  osKernelInitialize();

  /* USER CODE BEGIN RTOS_MUTEX */
  /* add mutexes, ... */
  /* USER CODE END RTOS_MUTEX */

  /* USER CODE BEGIN RTOS_SEMAPHORES */
  /* add semaphores, ... */
  /* USER CODE END RTOS_SEMAPHORES */

  /* USER CODE BEGIN RTOS_TIMERS */
  /* start timers, add new ones, ... */
  /* USER CODE END RTOS_TIMERS */

  /* USER CODE BEGIN RTOS_QUEUES */
  /* add queues, ... */
  /* USER CODE END RTOS_QUEUES */

  /* Create the thread(s) */
  /* creation of defaultTask */
  defaultTaskHandle = osThreadNew(StartDefaultTask, NULL, &defaultTask_attributes);

  /* creation of ltc_task */
  ltc_taskHandle = osThreadNew(start_ltc_function, NULL, &ltc_task_attributes);

  /* creation of soc_update_task */
  soc_update_taskHandle = osThreadNew(start_soc_function, NULL, &soc_update_task_attributes);

  /* creation of balance_task */
  balance_taskHandle = osThreadNew(start_balance_function, NULL, &balance_task_attributes);

  /* creation of comm_err_task */
  comm_err_taskHandle = osThreadNew(start_comm_err_function, NULL, &comm_err_task_attributes);

  /* USER CODE BEGIN RTOS_THREADS */
  /* add threads, ... */
  /* USER CODE END RTOS_THREADS */

  /* USER CODE BEGIN RTOS_EVENTS */
  /* add events, ... */


  osDelay(2000);
  HAL_GPIO_WritePin(EFUSE_GPIO_Port, EFUSE_Pin, GPIO_PIN_SET);
  HAL_TIM_Base_Start_IT(&htim3);
  HAL_TIM_Base_Start(&htim6);
  HAL_TIM_Base_Start(&htim8);


  HAL_ADCEx_Calibration_Start(&hadc1, ADC_SINGLE_ENDED);
  HAL_ADCEx_Calibration_Start(&hadc2, ADC_SINGLE_ENDED);

  HAL_ADC_Start_DMA(&hadc1, (uint32_t*)data.temperatures.adc, MAX_NUMBER_OF_TEMPERATURES);
  HAL_ADC_Start_DMA(&hadc2, (uint32_t*)data.current.adc, NUMBER_OF_CS_SAMPLES);

  /* USER CODE END RTOS_EVENTS */

  /* Start scheduler */
  osKernelStart();

  /* We should never get here as control is now taken by the scheduler */

  /* Infinite loop */
  /* USER CODE BEGIN WHILE */




  while (1)
  {
    /* USER CODE END WHILE */

    /* USER CODE BEGIN 3 */
  }
  /* USER CODE END 3 */
}

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
/* USER CODE BEGIN Header_StartDefaultTask */
/**
  * @brief  Function implementing the defaultTask thread.
  * @param  argument: Not used
  * @retval None
  */
/* USER CODE END Header_StartDefaultTask */
void StartDefaultTask(void *argument)
{
  /* init code for USB_DEVICE */
  MX_USB_DEVICE_Init();
  /* USER CODE BEGIN 5 */
  /* Infinite loop */
  for(;;)
  {
    osDelay(20);
  }
  /* USER CODE END 5 */
}

/**
  * @brief  Period elapsed callback in non blocking mode
  * @note   This function is called  when TIM16 interrupt took place, inside
  * HAL_TIM_IRQHandler(). It makes a direct call to HAL_IncTick() to increment
  * a global variable "uwTick" used as application time base.
  * @param  htim : TIM handle
  * @retval None
  */
void HAL_TIM_PeriodElapsedCallback(TIM_HandleTypeDef *htim)
{
  if (htim->Instance == TIM16) {
    HAL_IncTick();
  }
}

/**
  * @brief  This function is executed in case of error occurrence.
  * @retval None
  */
void Error_Handler(void)
{
  /* USER CODE BEGIN Error_Handler_Debug */
  /* User can add his own implementation to report the HAL error return state */
  __disable_irq();
  while (1)
  {
  }
  /* USER CODE END Error_Handler_Debug */
}

#ifdef  USE_FULL_ASSERT
/**
  * @brief  Reports the name of the source file and the source line number
  *         where the assert_param error has occurred.
  * @param  file: pointer to the source file name
  * @param  line: assert_param error line source number
  * @retval None
  */
void assert_failed(uint8_t *file, uint32_t line)
{
  /* USER CODE BEGIN 6 */
  /* User can add his own implementation to report the file name and line number,
     ex: printf("Wrong parameters value: file %s on line %d\r\n", file, line) */
  /* USER CODE END 6 */
}
#endif /* USE_FULL_ASSERT */

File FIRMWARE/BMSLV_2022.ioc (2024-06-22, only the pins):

Mcu.UserName=STM32L4P5RETx
PA11.Signal=USB_OTG_FS_DM
PA12.Signal=USB_OTG_FS_DP
PA2.GPIO_Label=EFUSE
PA2.Signal=GPIO_Output
PA3.GPIO_Label=THERM_1
PA3.Signal=ADCx_IN8
PA4.GPIO_Label=THERM_2
PA4.Signal=ADCx_IN9
PA5.GPIO_Label=THERM_3
PA5.Signal=ADCx_IN10
PA6.GPIO_Label=THERM_4
PA6.Signal=ADCx_IN11
PA7.GPIO_Label=THERM_5
PA7.Signal=ADCx_IN12
PB0.GPIO_Label=THERM_8
PB0.Signal=ADCx_IN15
PB1.GPIO_Label=CURRENT_SENSOR
PB1.Signal=ADCx_IN16
PB11.GPIO_Label=FUSE_VOLTAGE
PB11.Signal=GPIO_Output
PB2.GPIO_Label=INTERLOCK
PB2.Signal=GPIO_Input
PB5.Signal=SPI1_MOSI
PB8.Signal=CAN1_RX
PB9.Signal=CAN1_TX
PC4.GPIO_Label=THERM_6
PC4.Signal=ADCx_IN13
PC5.GPIO_Label=THERM_7
PC5.Signal=ADCx_IN14
PC6.GPIO_Label=LED_1
PC6.Signal=GPIO_Output
PC7.GPIO_Label=LED_2
PC7.Signal=GPIO_Output
PC8.GPIO_Label=LED_3
PC8.Signal=GPIO_Output
PC9.GPIO_Label=LED_4
PC9.Signal=GPIO_Output

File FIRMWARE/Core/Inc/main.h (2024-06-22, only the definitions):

#define EFUSE_Pin GPIO_PIN_2
#define EFUSE_GPIO_Port GPIOA
#define THERM_1_Pin GPIO_PIN_3
#define THERM_1_GPIO_Port GPIOA
#define THERM_2_Pin GPIO_PIN_4
#define THERM_2_GPIO_Port GPIOA
#define THERM_3_Pin GPIO_PIN_5
#define THERM_3_GPIO_Port GPIOA
#define THERM_4_Pin GPIO_PIN_6
#define THERM_4_GPIO_Port GPIOA
#define THERM_5_Pin GPIO_PIN_7
#define THERM_5_GPIO_Port GPIOA
#define THERM_6_Pin GPIO_PIN_4
#define THERM_6_GPIO_Port GPIOC
#define THERM_7_Pin GPIO_PIN_5
#define THERM_7_GPIO_Port GPIOC
#define THERM_8_Pin GPIO_PIN_0
#define THERM_8_GPIO_Port GPIOB
#define CURRENT_SENSOR_Pin GPIO_PIN_1
#define CURRENT_SENSOR_GPIO_Port GPIOB
#define INTERLOCK_Pin GPIO_PIN_2
#define INTERLOCK_GPIO_Port GPIOB
#define FUSE_VOLTAGE_Pin GPIO_PIN_11
#define FUSE_VOLTAGE_GPIO_Port GPIOB
#define LED_1_Pin GPIO_PIN_6
#define LED_1_GPIO_Port GPIOC
#define LED_2_Pin GPIO_PIN_7
#define LED_2_GPIO_Port GPIOC
#define LED_3_Pin GPIO_PIN_8
#define LED_3_GPIO_Port GPIOC
#define LED_4_Pin GPIO_PIN_9
#define LED_4_GPIO_Port GPIOC
#define SW_DIO_Pin GPIO_PIN_13
#define SW_DIO_GPIO_Port GPIOA
#define SW_CLK_Pin GPIO_PIN_14
#define SW_CLK_GPIO_Port GPIOA
#define SPI1_CS_Pin GPIO_PIN_15
#define SPI1_CS_GPIO_Port GPIOA

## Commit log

2021-11-12 gitinit for c++/kicad
2021-11-22 Hardware Update 1
    +CAN section
    +LTC6810 section
    +Thermistors section
    [BMS_LV_2022.kicad_pcb, BMS_LV_2022.sch, Balance.sch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]
2021-11-29 Hardware Update 2
    First verison of the scheme finished
    +Power section
    +eFuse section
    +Current Sensor section
    +Connectors section
    +Debug LEDs
    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
    [BMS_LV_2022.sch, Balance.sch, CAN.sch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]
2021-12-13 Hardware update; -changes after team review;
    [BMS_LV_2022.kicad_pcb, BMS_LV_2022.sch, CurrentSensor.sch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]
2021-12-14 Electrical Rules Checker fixes
    [BMS_LV_2022.sch, Balance.sch, CAN.sch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]
2021-12-15 Most of the footprints added
    [BMS_LV_2022.sch, Balance.sch, CAN.sch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]
2021-12-17 PCB layout init
    [BMS_LV_2022.kicad_pcb, BMS_LV_2022.sch, LTC6810.sch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]
2021-12-31 Thermistors change
    [BMS_LV_2022.kicad_pcb, Balance.sch, CAN.sch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]
2022-01-09 PCB update
    Parts changed due to smaller footprints
    [BMS_LV_2022.kicad_pcb, BMS_LV_2022.sch, Balance.sch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]
2022-01-14 PCB Layout Update
    Some work on PCB Layout
    + AS214-97PN (connector) 3D model added
    [AS214-97PN.STEP, BMS_LV_2022.kicad_pcb, Balance.sch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]
2022-01-14 PCB Layout Update 2
    [BMS_LV_2022.kicad_pcb]
2022-01-19 PCB Layout Update 3
    [3522-2.stp, BMS_LV_2022.kicad_pcb, BMS_LV_2022.sch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]
2022-01-19 Power planes added
    [BMS_LV_2022.kicad_pcb, BMS_LV_2022.sch, Balance.sch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]
2022-01-21 PCB Routing Update
    [BMS_LV_2022.kicad_pcb, BMS_LV_2022.sch, Balance.sch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]
2022-01-22 PCB Routing Update 2
    [BMS_LV_2022.kicad_pcb, BMS_LV_2022.sch, Balance.sch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]
2022-01-22 Small bug fixes
    [BMS_LV_2022.kicad_pcb, BMS_LV_2022.sch]
2022-01-23 Bug fixes on PCB
    [BMS_LV_2022.kicad_pcb]
2022-01-23 HARDWARE Release V1.0
    [BMS_LV_2022-B_Cu.gbr, BMS_LV_2022-B_Mask.gbr, BMS_LV_2022-B_Paste.gbr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]
2022-01-24 Changes in V1.0
    -Fuse holder change
    -Autosport conn angle change
    [3557-2.stp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]
2022-01-24 Last Changes in V1.0
    Fuse voltage measurement added
    [BMS_LV_2022-B_Cu.gbr, BMS_LV_2022-B_Mask.gbr, BMS_LV_2022-B_Paste.gbr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]
2022-03-15 Balance section -> specific transistor added
    [Balance.sch, CAN.sch, Power.sch]
2022-05-05 PCB test on 2021 code, FreeRTOS init
2022-05-13 Balance task
    -some changes in soc_update_task.cpp
    -first version of balance_task
    -Interlock pin added on PB2
    -Charging struct added
    -defines needed to balance_task added
2022-05-15 error handling
    HARDWARE:
    -transistor change (only proper name added)
    FIRMWARE:
    -error handling functions added
    -balance_task small changes
    -min_max_cell_voltage function changed to work on global variables
    [Balance.sch]
2022-05-17 ETL library
    -ETL library added
    -bug fixes
    -comm_err_task work in progress
    -soc class moved to global struct in main.h
    [balance_task.cpp]
2022-05-21 USB added, CAN Library added
    -USB added
    -CAN library added
    -serial communication function added
    -error checker finished
    -some small all-around changes
    [BMSLV_2022.ioc, balance_task.cpp, comm_err_task.cpp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]
2022-05-22 Renewed project
    Due to bugs I couldn't resolve, the new project has been created.
    -structs and defines were moved to new file
    -some small bugs were fixed
    [BMSLV_2022.ioc, balance_task.cpp, comm_err_task.cpp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]
2022-05-25 FIXES
    -DMA fixed (ioc changes)
    -FreeRTOS fixed (memory per task increased, osDelay in every task)
    -huge fix in current sensor section (I forgot about hardware voltage divider, so I added one on pcb- it looks bad but it works :); it will be an update with that in kicad)
    -can_function added
    -error task lift
    To sum up, verything looks fine, its like alpha version for some serious tests.
    [BMSLV_2022.ioc, balance_task.cpp, comm_err_task.cpp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]
2022-05-29 Charging interlock logic fixed
    [BMSLV_2022.ioc, balance_task.cpp, main.cpp]
2022-06-12 Small fixes
    balance_task -> balance algorythm fixed
    comm_err_task -> added ticks for every communication (serial, CANs)
    -temperature adc physically changed to other pins (Im using 5 temperature sensors in this case) by moving them in connector - thats why there is change in get_temperatures function; now adc 7-3 are valid and 2-0 arent
    [balance_task.cpp, comm_err_task.cpp, global_variables.hpp]
2022-06-22 Code review fixes, CAN library update
    -few fixes after code review
    -CAN Library update
    [balance_task.cpp, comm_err_task.cpp, global_variables.hpp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]
2022-06-27 min_max_voltage fixed
    +small changes in balance task
    [balance_task.cpp, global_variables.hpp]
2022-06-27 Voltage divider in current sensor section added
    [BMS_LV_2022.kicad_pcb, Balance.sch, CurrentSensor.sch]
2022-08-03 temperature measurement disconnection error implemented
    [comm_err_task.cpp]
2024-03-28 Adding the main condition: battery balancing starts when the interlock is plugged in and a signal from USB "BB_Start" is received
2024-04-04 Code review
    +error check also on command added
    +bool to balance flag added
    [comm_err_task.cpp, global_variables.hpp]
2024-04-04 Comm Err Task
    changing the conditions that trigger the error-finding and response functions
    [comm_err_task.cpp]
2024-04-04 Balance Task
    Changing the conditions for invoking the battery balancing system
2024-04-09 Receiving messages from USB
    improved code for reading and comparing commands coming from USB
    BB_Start -> data.charging.balance_on = true
    BB_Stop -> data.charging.balance_on = false
2024-04-29 Update project to KiCad 8.0
    [BMS_LV_2022.kicad_pcb, BMS_LV_2022.kicad_sch, BMS_LV_2022.sch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]
2024-04-29 New fuses and programming connector added
    [0154010.DR.stp, BMS_LV_2022.kicad_pcb, BMS_LV_2022.kicad_sch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]
2024-04-29 Significant changes
    -main connector changed to the other side of the pcb because of using socket connector in the new version
    -changed usb mini to usb-c
    -changed fuse to 2 fuses protecting current path pins separately
    -some minor changes in layout
    [BMS_LV_2022.kicad_pcb, BMS_LV_2022.kicad_sch, CAN.kicad_sch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]
2024-04-30 Version 2.0
    Grounding corrected and production files added
    [BMS_LV_2022.kicad_pcb]
2024-06-22 CubeIDE migration to latest version, rest of the changes in description
    - clock changed from external oscillator to internal (HSE->HSI) due to some errors (might be a hardware problem but it's hard to change it now when it's on the battery stack already)
    - temperatures measurement changed from 5 to 8 as the battery now is bigger and all the measurements are needed
    [bom_bmslv.ods]
2024-10-03 FS Poland 2024
    - neutral current sleep commented - it's not good on competition
    - lack of error check when the charger is connected commented
    [comm_err_task.cpp]
2024-10-12 Ability to enable and disable errors using a UART command
    [comm_err_task.cpp, global_variables.hpp]
2024-10-12 Add default error detection enabled
    [comm_err_task.cpp]
2024-10-27 Add display information on UART about status BB and error detect
    [comm_err_task.cpp]
2024-11-26 Edit symbols in Autosport Connector footprint
    [BMS_LV_2022.kicad_sch, Balance.kicad_sch, CAN.kicad_sch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]
2024-11-30 Autosport connector scheme updated
    [BMS_LV_2022.kicad_pcb, BMS_LV_2022.kicad_sch, Balance.kicad_sch]

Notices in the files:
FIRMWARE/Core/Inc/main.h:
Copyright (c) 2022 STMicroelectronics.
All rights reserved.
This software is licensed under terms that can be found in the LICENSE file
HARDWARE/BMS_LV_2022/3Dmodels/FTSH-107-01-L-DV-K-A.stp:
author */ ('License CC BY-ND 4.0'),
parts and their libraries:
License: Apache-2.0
